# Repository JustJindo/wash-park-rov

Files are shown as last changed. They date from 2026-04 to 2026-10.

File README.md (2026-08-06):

I love ROVs, so I'm making one of my own. My ROV's going to dive to the bottom of Smith Lake in Denver, CO's Washington Park. I created this repository to  record my work and familiarize myself with Git in the process.
If you share an interest in making ROVs, I hope this repository's contents can be of some value to you.

Here's how my ROV looks as of March 27.
Here's an update on the ROV as of June 4.
ROV propulsion system is nearly finished as of June 6.

UPDATE 06/13/2026: I tested the first working prototype of my ROV in Smith Lake today! My ROV made it to the bottom of the lake, just upside down. There are a number of buoyancy issues to be addressed, and some water got into the enclosure from an unknown point of vulnerability. Fortunately, all the electronics somehow survived my ROV's first trial run, and I've identified A LOT of new considerations for my next prototype. Here's some [video](https://www.dropbox.com/scl/fi/9tpkhjxywr2wt594vu4l5/washparkrov_0613.mov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) from a GoPro I stuck in the ROV's dome port.

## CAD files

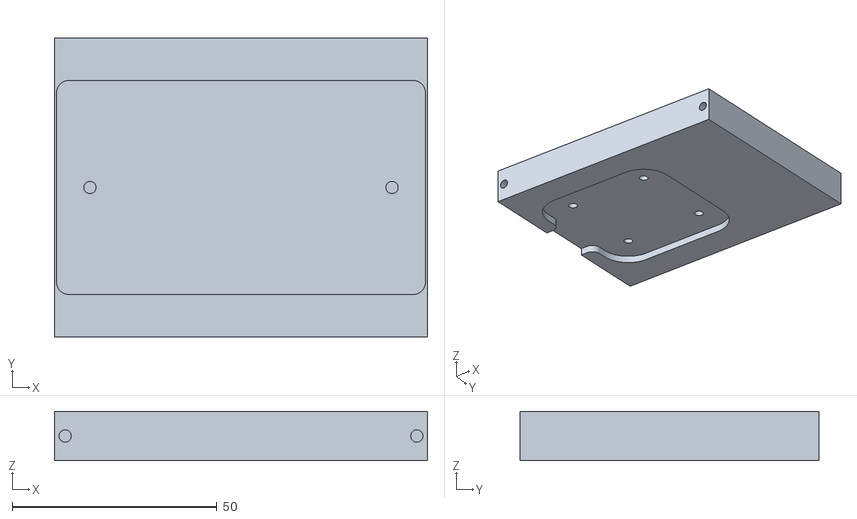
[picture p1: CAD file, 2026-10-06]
mk2_models/tray_v1.stl
91.0 x 73.0 x 12.0

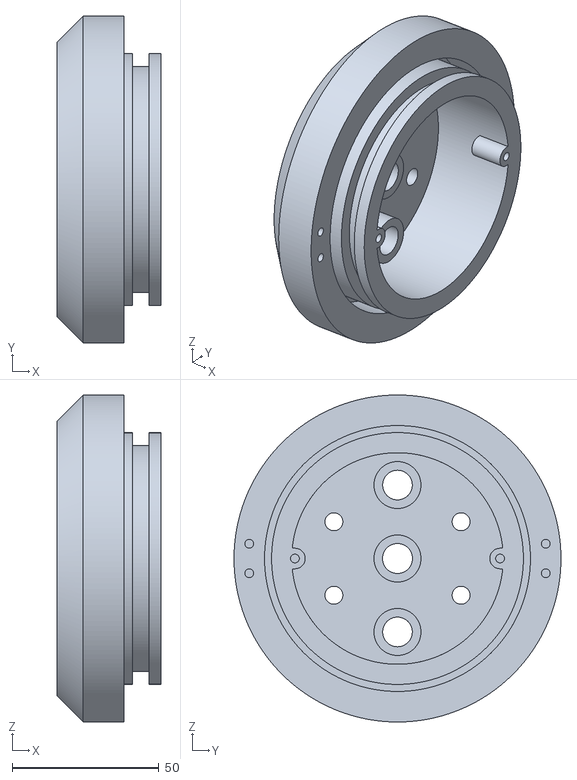
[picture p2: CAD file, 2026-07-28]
mk2_models/rearcap_v3.stl
35.6 x 111.3 x 111.3

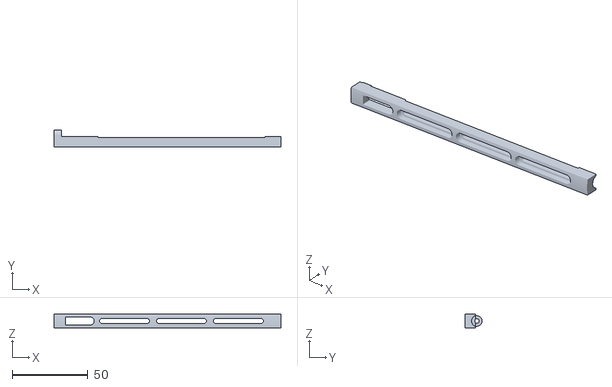
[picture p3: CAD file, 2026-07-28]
mk2_models/rail_star_v1.stl
149.6 x 11.4 x 9.00

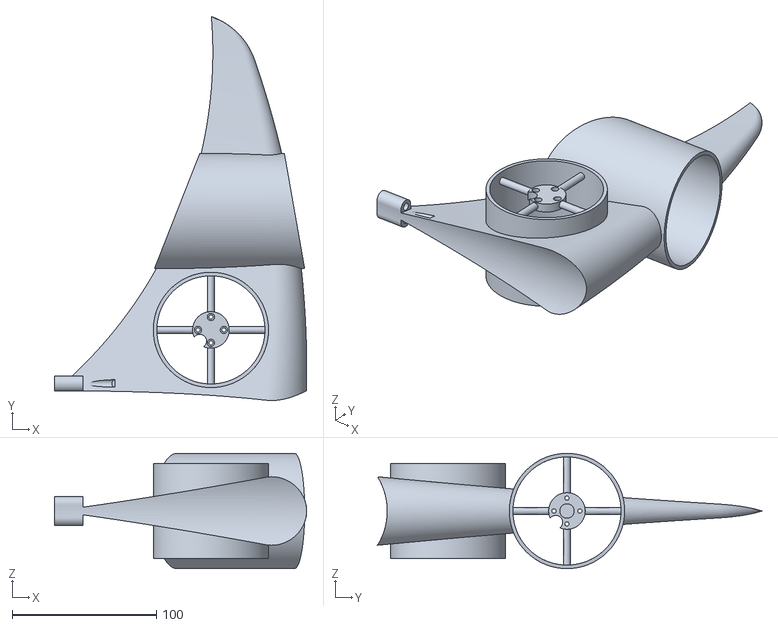
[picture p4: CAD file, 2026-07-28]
mk2_models/wing_port_v1.stl
175.2 x 266.5 x 80.0

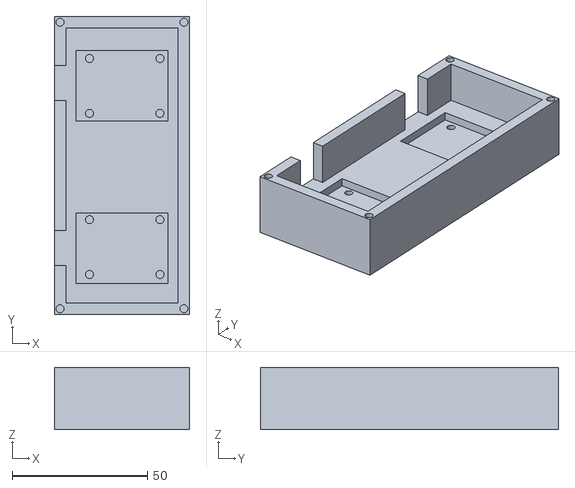
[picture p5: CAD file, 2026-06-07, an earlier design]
mk1_models/controller_base_v3.stl
50.0 x 110.0 x 23.0

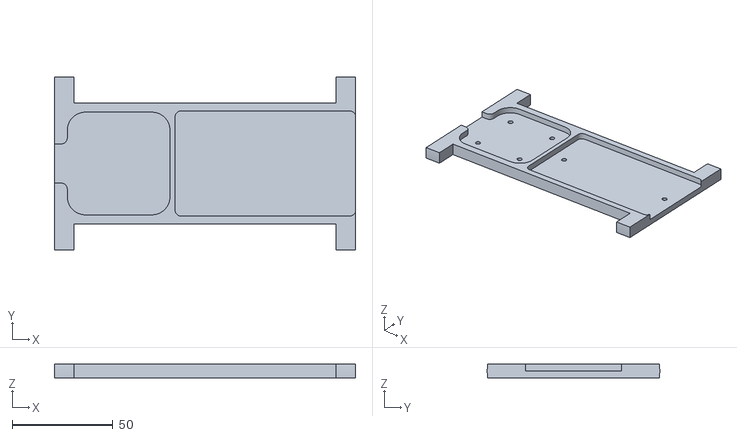
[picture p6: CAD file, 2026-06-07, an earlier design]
mk1_models/tray_v4.stl
149.5 x 85.7 x 7.00

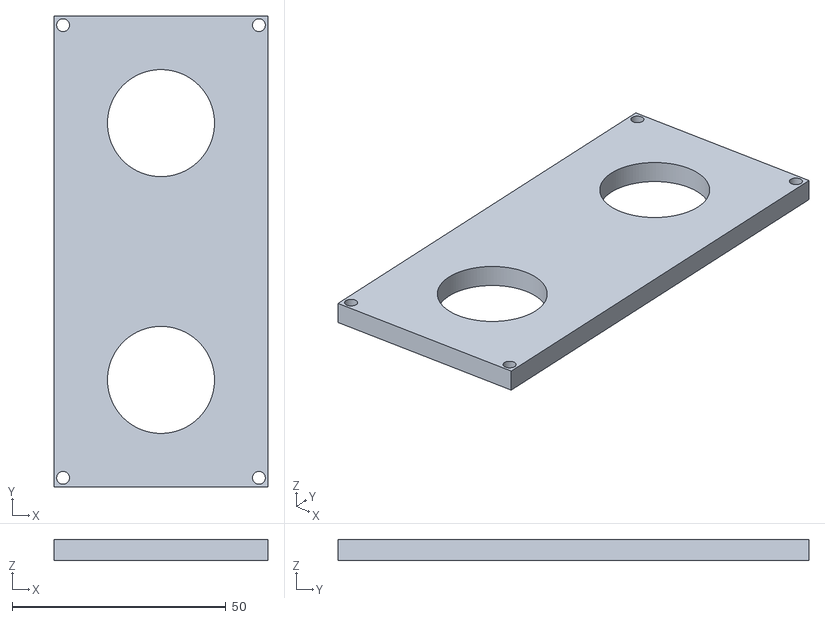
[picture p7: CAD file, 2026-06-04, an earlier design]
mk1_models/controller_panel_v2.stl
50.0 x 110.0 x 5.00

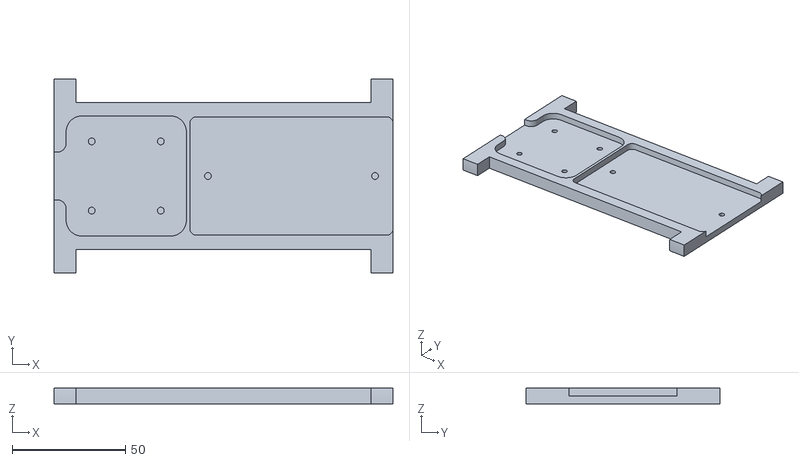
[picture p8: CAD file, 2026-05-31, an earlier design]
mk1_models/tray_v2.stl
149.5 x 85.7 x 7.00

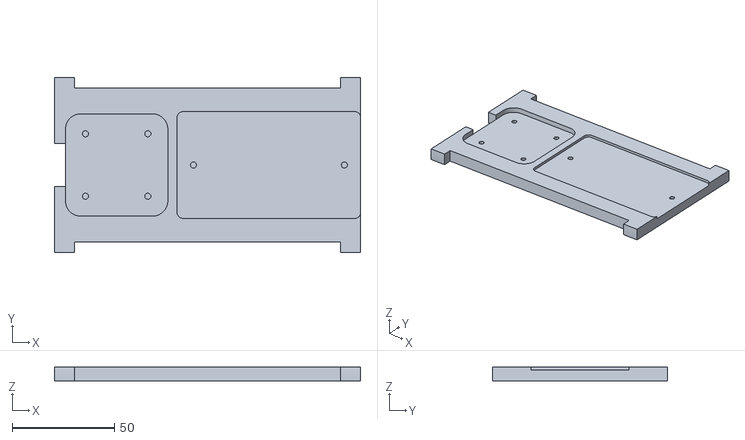
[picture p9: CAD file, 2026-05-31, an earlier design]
mk1_models/tray_v1.stl
149.5 x 85.7 x 7.00

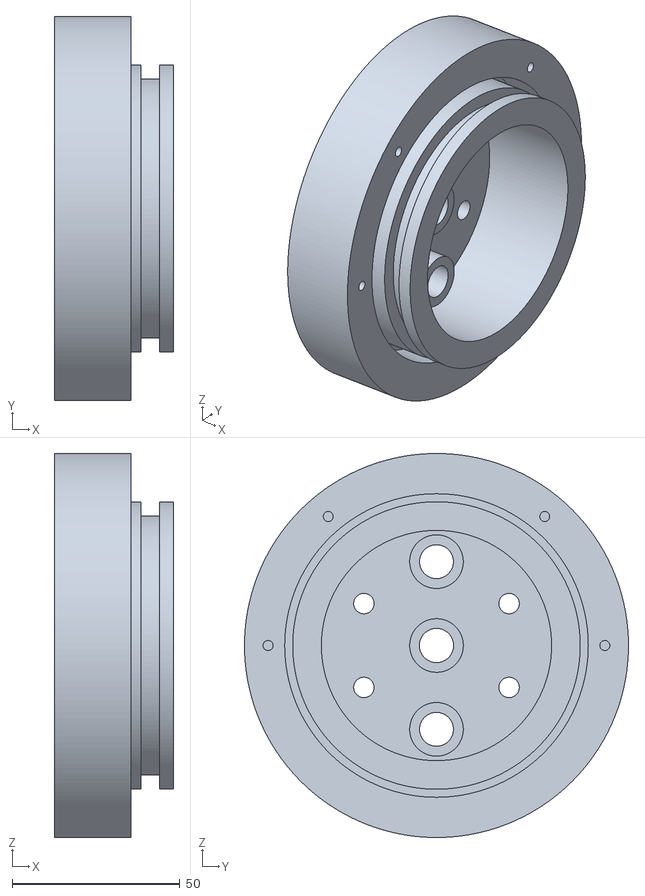
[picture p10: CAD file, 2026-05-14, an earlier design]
mk1_models/rearcap_v2.stl
35.6 x 114.5 x 114.5

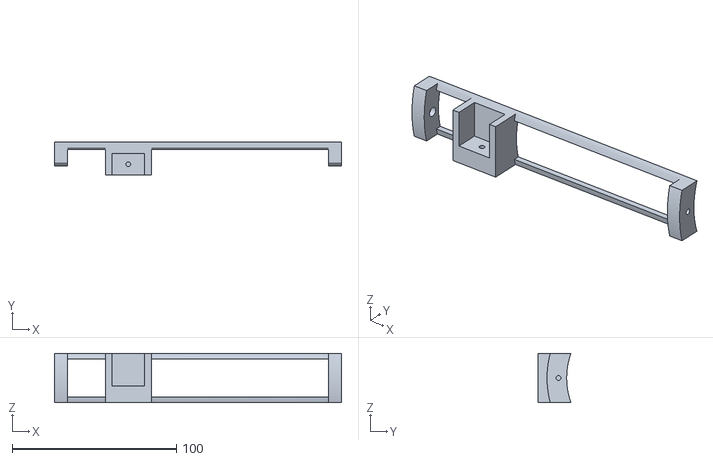
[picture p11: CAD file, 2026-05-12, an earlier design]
mk1_models/arm_vt_star_v1.stl
175.0 x 20.0 x 30.0

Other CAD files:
mk2_models/rail_port_v1.stl
mk2_models/wing_star_v1.stl
mk1_models/controller_base_v2.stl
mk1_models/tray_v3.stl
mk1_models/controller_panel_v1.stl
mk1_models/controller_base_v1.stl
mk1_models/rearcap_v1.stl
mk1_models/arm_ht_v1.stl
mk1_models/arm_vt_port_v1.stl
mk1_models/brace_v2.stl
mk1_models/frontcap_v2.stl
mk1_models/frontcap_v3.stl
mk1_models/frontcap_v4.stl
mk1_models/propeller_ccw_v4.stl
mk1_models/propeller_ccw_v5.stl
mk1_models/propeller_cw_v5.stl
mk1_models/rov_v1.f3z
mk1_models/shroud_v2.stl
mk1_models/shroud_v3.stl
mk1_models/shroud_v4.stl

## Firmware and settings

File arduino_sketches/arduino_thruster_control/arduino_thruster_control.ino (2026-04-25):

/* Motor Control w/ Joystick
 *
 * This program uses two joysticks to control 3 DC motors driven by
 * an Adafruit Motor Shield v3.
 * Left joystick controls horizontal (FORWARD, BACK, RIGHT, LEFT) thrusters.
 * Right joystick controls vertical (UP, DOWN) thruster.
 */

#include <stdio.h>
#include <Adafruit_MotorShield.h>

// MOTOR NEEDS SEPARATE VOLTAGE SUPPLY

// create motor shield object w/ default I2C address
Adafruit_MotorShield AFMS = Adafruit_MotorShield();
// set left motor to port M1, right motor to port M2
Adafruit_DCMotor *leftMotor = AFMS.getMotor(1);
Adafruit_DCMotor *rightMotor = AFMS.getMotor(2);
Adafruit_DCMotor *vertMotor = AFMS.getMotor(3);

// pins A0, A1 are connected to left joystick's analog outputs
#define leftXPin       A0
#define leftYPin       A1
// pin 7 is connected to left joystick's button
#define leftButtonPin  7
// pins A2, A3 are connected to right joystick's analog outputs
#define rightXPin      A2
#define rightYPin      A3
// pin 4 is connected to right joystick's button
#define rightButtonPin 4

void setup() {

  // set button pins to be active low
  pinMode(leftButtonPin, INPUT_PULLUP);
  pinMode(rightButtonPin, INPUT_PULLUP);
  // begin serial communication at 9600 bits per sec
  Serial.begin(9600);
  Serial.println("Starting program...");

  // begin motor shield operation w/ default frequency (1.6kHz)
  if(!AFMS.begin()) {
    Serial.println("Could not find motor shield. Check wiring...");
    while(1);
  } // end if
  Serial.println("Motor shield found.");

} // end setup

void loop() {

  // read joystick values from pins
  int leftXValue = analogRead(leftXPin);
  int leftYValue = analogRead(leftYPin);
  int leftButtonValue = digitalRead(leftButtonPin);
  int rightXValue = analogRead(rightXPin);
  int rightYValue = analogRead(rightYPin);
  int rightButtonValue = digitalRead(rightButtonPin);
  // save max PWM to pass when running motors
  int motorPWM =  255;

  // NOTE: Horizontal and vertical thrusters should be controlled 
  //       independently if you want to run them simultaneously.

  // if right joystick is pushed forward
  if(rightYValue < 300) {
    vertMotor->run(BACKWARD);
    vertMotor->setSpeed(motorPWM);
  } // else if right joystick is pushed backward
  else if(rightYValue > 700) {
    vertMotor->run(FORWARD);
    vertMotor->setSpeed(motorPWM);
  } // else don't run vertical motor
  else {
    vertMotor->run(RELEASE);
  } // end else

  // if left joystick is pushed forward
  if(leftYValue < 300) {
    leftMotor->run(FORWARD);
    leftMotor->setSpeed(motorPWM);
    rightMotor->run(FORWARD);
    rightMotor->setSpeed(motorPWM);
  } // else if left joystick pushed backward
  else if(leftYValue > 700) {
    leftMotor->run(BACKWARD);
    leftMotor->setSpeed(motorPWM);
    rightMotor->run(BACKWARD);
    rightMotor->setSpeed(motorPWM);
  } // else if left joystick is pushed right
  else if(leftXValue > 700) {
    leftMotor->run(FORWARD);
    leftMotor->setSpeed(motorPWM);
    rightMotor->run(BACKWARD);
    rightMotor->setSpeed(motorPWM);
  } // else if left joystick is pushed left
  else if(leftXValue < 300) {
    leftMotor->run(BACKWARD);
    leftMotor->setSpeed(motorPWM);
    rightMotor->run(FORWARD);
    rightMotor->setSpeed(motorPWM);
  }  // else don't run horizontal motors
  else {
    leftMotor->run(RELEASE);
    rightMotor->run(RELEASE);
  } // end else 

  Serial.print(leftXValue);
  Serial.print("\t");
  Serial.print(leftYValue);
  Serial.print("\t");
  Serial.print(leftButtonValue);
  Serial.print("\t");
  Serial.print(rightXValue);
  Serial.print("\t");
  Serial.print(rightYValue);
  Serial.print("\t");
  Serial.print(rightButtonValue);
  Serial.println("");

  // 10 ms delay for stability
  delay(10);

} // end loop

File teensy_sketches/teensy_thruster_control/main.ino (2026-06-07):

#include <stdio.h>
// include Teensy servo library
#include <PWMServo.h>

// A14 = 38, A15 = 39, A16 = 40, A17 = 41
#define leftXPin 40
#define leftYPin 41
#define leftButtonPin 36
#define rightXPin 38
#define rightYPin 39
#define rightButtonPin 37

/*POTENTIOMETER AXES ORIENTATIONS IN CONTROLLER
  LEFT: Y->1024
  RIGHT: Y->0
  UP: X->0
  DOWN: X->1024
  
  M1 = Port Side Horizontal
  M2 = Port Side Vertical
  M3 = Starboard Side Horizontal
  M4 = Starboard Side Vertical*/
  
#define M1_signalPin 2
#define M2_signalPin 3
#define M3_signalPin 4
#define M4_signalPin 5

/*APISQUEEN 12-24V 45A Bi-directional ESC
  >500Hz Refresh
  1-2ms PWM Signal
  1.5-2ms Forward
  1-1.5ms Backward
  1.5ms Zero Throttle*/

void setup() {
  // set PWM frequency to 500 Hz
  analogWriteFrequency(M1_signalPin, 500);
  analogWriteFrequency(M2_signalPin, 500);
  analogWriteFrequency(M3_signalPin, 500);
  analogWriteFrequency(M4_signalPin, 500);
  // set pulse width resolution to 8 bits
  analogWriteResolution(8);
  // begin serial communication at 9600 bits/sec
  Serial.begin(9600);
  // 3 second delay written into calibration for stability
  calibrate_esc(M1_signalPin);
  calibrate_esc(M2_signalPin);
  calibrate_esc(M3_signalPin);
  calibrate_esc(M4_signalPin);
} // end setup

/*
Relationship between value sent to signal pin and resultduty cycle is described below:
W Pulse Width
C Control Signal
R Resolution
F Frequency
W = C / R*F
W = C / 256*500
*/

void loop() {
  // read joystick values from pins
  int leftXValue = analogRead(leftXPin);
  int leftYValue = analogRead(leftYPin);
  int leftButtonValue = digitalRead(leftButtonPin);
  int rightXValue = analogRead(rightXPin);
  int rightYValue = analogRead(rightYPin);
  int rightButtonValue = digitalRead(rightButtonPin);

  // map potentiometer axes ranging from 0-1023 to a valid pulse width range from 128-255
  int leftXPWM = map(leftXValue, 0, 1023, 128, 255);
  int leftYPWM = map(leftYValue, 0, 1023, 128, 255);
  int rightXPWM = map(rightXValue, 0, 1023, 128, 255);
  int rightYPWM = map(rightYValue, 0, 1023, 128, 255);

   // LEFT JOYSTICK FORWARD/BACKWARD
  // if axis value passes deadzone, write pulse width to respective signal pin(s)
  if(leftXValue > 524 || leftXValue < 500) {
    analogWrite(M1_signalPin, leftXPWM);
    analogWrite(M3_signalPin, leftXPWM - 2*(leftXPWM - 191));
  } // end if
  // NEUTRAL
  // else, set thruster(s) to neutral
  else {
    analogWrite(M1_signalPin, 191);
    analogWrite(M3_signalPin, 191);
  } // end else
  
  // RIGHT JOYSTICK FORWARD/BACKWARD
  if(rightXValue > 524 || rightXValue < 500) {
    analogWrite(M2_signalPin, rightXPWM);
    analogWrite(M4_signalPin, rightXPWM - 2*(rightXPWM - 191));
  } // end if
  // RIGHT JOYSTICK LEFT/RIGHT
  else if(rightYValue > 524 || rightYValue < 500) {
    analogWrite(M1_signalPin, rightYPWM);
    analogWrite(M3_signalPin, rightYPWM);
  } // end else if
  // NEUTRAL
  else{
    analogWrite(M2_signalPin, 191);
    analogWrite(M4_signalPin, 191);
  } // end else

  Serial.print(leftXValue);
  Serial.print("\t");
  Serial.print(leftYValue);
  Serial.print("\t");
  Serial.print(leftButtonValue);
  Serial.print("\t");
  Serial.print(rightXValue);
  Serial.print("\t");
  Serial.print(rightYValue);
  Serial.print("\t");
  Serial.print(rightButtonValue);
  Serial.println("");

  // 10 ms delay for stability
  delay(10);
} // end loop

// calibrate ESC by sending 1.5ms signal for zero throttle at power on, then forward throttle, then backward.
void calibrate_esc(int signalPin) {
  Serial.println("Calibrating ESCs...");

  // begin at zero throttle for three seconds
  analogWrite(signalPin, 192);
  delay(3000);
  // send forward throttle for one second
  Serial.println("Forwards...");
  analogWrite(signalPin, 255);
  delay(1000);
  // return to zero throttle for one second
  Serial.println("Pause...");
  analogWrite(signalPin, 192);
  delay(1000);
  // send backward throttle for one second
  Serial.println("Backwards...");
  analogWrite(signalPin, 128);
  delay(1000);
  // return to zero throttle
  analogWrite(signalPin, 192);

  Serial.println("Calibration complete.");
  delay(3000);
} //end calibrate_esc

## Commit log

2026-04-23 Moved local files from new ROV project to repository.
    I've been locally storing files related to my new ROV on a folder in my desktop. Now these files have been moved to my repository for the Wash Park ROV project.
    [brace_v2.stl, frontcap_v2.stl, frontcap_v3.stl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]
2026-04-25 Labeled files by board.
    Available libraries differ between Arduino Uno and Teensy 4.1 based on hardware. I think it's best to identify which of my files were written for which board.
2026-04-25 Renamed parts folder.
    [brace_v2.stl, frontcap_v2.stl, frontcap_v3.stl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]
2026-04-25 Create teensy_thruster_control.ino
    Created sketch for full thruster control with Teensy 4.1.
2026-04-27 Labeled propeller files by orientation.
    Propeller files are now distinguished by CW/CCW blade orientation.
    [propeller_v4_ccw.stl, propeller_v5_ccw.stl, propeller_v5_cw.stl]
2026-04-27 Added potentiometer values readout. Added parameter to calibrate_esc function.
    Defined potentiometer pins, main loop prints out values read from potentiometer axes. Added parameter to calibrate_esc function to perform calibration with different signal pins.
2026-05-02 Renamed propeller files to list orientation first.
    [propeller_ccw_v4.stl, propeller_ccw_v5.stl, propeller_cw_v5.stl]
2026-05-02 Added final versions of parts.
    [arm_ht_v1.stl, arm_vt_v1.stl, portHTarm_v1.stl]
2026-05-04 Updated brace print settings.
2026-05-04 Added rear endcap model.
    [rearcap_v1.stl]
2026-05-06 Added cut for motor hub.
    [shroud_v4.stl]
2026-05-07 Added pressure relief valve bulkhead to rear endcap.
    [rearcap_v1.stl]
2026-05-12 Labeled arm models by side.
    [arm_vt_port_v1.stl, arm_vt_star_v1.stl, arm_vt_v1.stl]
2026-05-14 Updated rear endcap design.
    Thinned bulkhead wall for cable penetrator passage.
    [rearcap_v2.stl]
2026-05-14 Removed .gcode files.
    .gcode files don't need to be included as long as .stl files are available, so I've removed them.
2026-05-19 Added threshold for thruster activation in teensy_esc_test.ino.
    Added potentiometer threshold values for sending forward/reverse signals to the thruster. Thruster is now immobile unless the joystick is pushed forwards/backwards to a sufficient extent.
    [teensy_esc_test.ino]
2026-05-27 Added controls for all thrusters to teensy_thruster_control.ino.
    Added thruster control with left and right joysticks for lateral and vertical propulsion.
2026-05-31 Updated electronics tray.
    Deepened component extrusions and cable passages on both sides.
    [tray_v1.stl, tray_v2.stl]
2026-06-04 Created model for handheld joystick controller.
    Modelled first version of a handheld controller to comfortably host both joysticks.
    [controller_base_v1.stl, controller_panel_v1.stl]
2026-06-04 Resized slot for power distribution hub.
    Reduced lengths of slots for power distribution hub and its main power leads. Increased lengths of fillets.
    [tray_v3.stl]
2026-06-04 Updated handheld controller models.
    Moved joysticks off center of boards, widened joystick holes. Adjusted joystick boards' fasteners.
    [controller_base_v2.stl, controller_panel_v2.stl]
2026-06-07 Resized PDB slot and respective fillets.
    Shortened length of power distribution slot's sides. Narrowed fillets at corners.
    [tray_v4.stl]
2026-06-07 Adjusted position of left joystick slot.
    Moved left joystick slot closer to center of controller. Joystick potentiometers have identical positions on board.
    [controller_base_v3.stl]
2026-06-07 Added yaw to propulsion controls. Reduced potentiometers' deadzones.
    Revised joystick controls for positions in handheld controller. Added yaw for rotational motion. Joysticks have been recentered to ~500 bits at neutral, so deadzones have been reduced.
2026-06-30 Archived first version of ROV.
    ROV frame will be completely redesigned, so I exported the first modeled prototype to an archive file.
    [rov_v1.f3z]
